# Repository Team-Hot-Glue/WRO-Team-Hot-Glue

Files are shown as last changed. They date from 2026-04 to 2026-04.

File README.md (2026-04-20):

# WRO-KU-STEAM-Hot-Glue

Hello and welcome to our repository :D

Here you will find all the code and CAD files for our robot, as well as the engineering journal that dives into how we made it.

**Assembly instructions**

**1)** In **CAD files -> Current_build** there is a .step file of the full robot assembly. It contains all the custom-made parts of the chassis. You can import it into CAD software of your choice and view how the robot's fully assembled chassis must look like. We recommend using it as a reference during assembly.  

**2)** 3D Print the provided .stl files using PLA or PETG. *Note*: we also used a metal Makeblock mBot2 chassis. This chasis part can be bought on online retailers like AliExpress or just salvaged from a broken mBot2 (that's what we did). You could also 3D print the chassis and modify it as we did (written bellow). You can buy the 3D file here (just keep in mind that the plastic version is likelly going to perform worse then the metal):  https://sketchfab.com/3d-models/mbot2-chassis-36600557720d4e2c9568bb747af69cdd
* DISCLAIMER - We are not the authors of this file and are not associated with the seller of the 3D file. We just provide an option to 3D print the chassis.
  
**3)** Chassis modification. We cut off the part of the chassis..... (Coming soon)    We spray painted it with some generic white car primer, that was found in a local hardware store for cheap (painting is completely optional, we did it just for looks).
  
**4)** Order the necessary electronic components from your local electronics components shop or an online retailer. The full list and rellevant links can be found **IN THE ENGINEERING JOURNAL**

**5)** Screw in the 3D printed parts to the chassis. Most of the screws used are M4 size (later the exact sizes and amounts of each size screws will be confirmed)

**6)** Mount the electronic components to the chassis. TOF sensors will need to be screwed in, motor board doesnt need screws, it is beeing held in place by tpu stoppers (you have to 3D print them, the file is provided). Raspberry pi is beeing held to the chassis by velcro tape (similar to this, but different manufacturer: https://www.amazon.com/Adhesion-Adhesive-Interlocking-Mounting-Reclosable/dp/B0F8QH6T7F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)

**7)** Connect all the cables according to the wiring diagram: **Wiring.pdf**

**8)** Cable manage everything. We used zipties and hotglue for that, to stop the header connectors and jumpers from disconecting CA glue was used.

**9)** Enjoy your new robot, make it pretty by adding cat stickers to it (optional, but highly recommended) 

wro cat

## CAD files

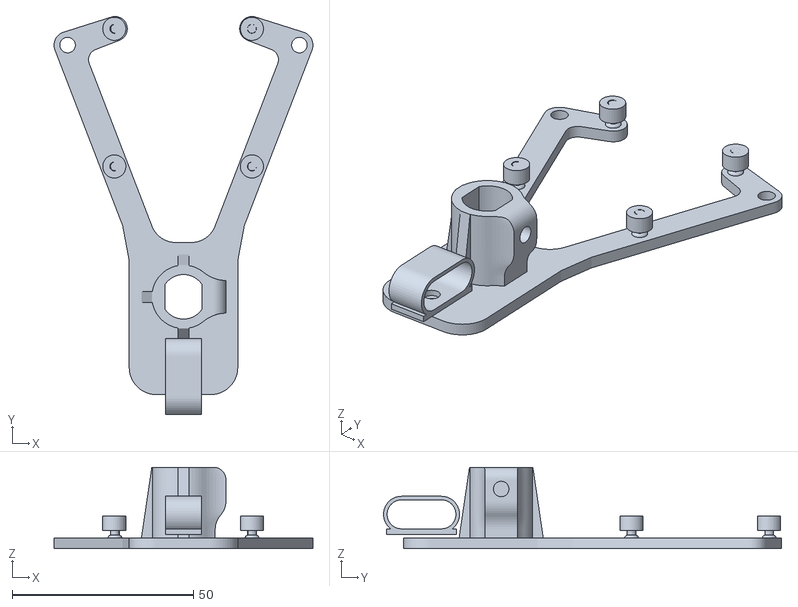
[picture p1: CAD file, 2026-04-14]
CAD files/Current_version/Files_for_printing/motor_housing_asmbl.stl
71.5 x 109.9 x 22.5

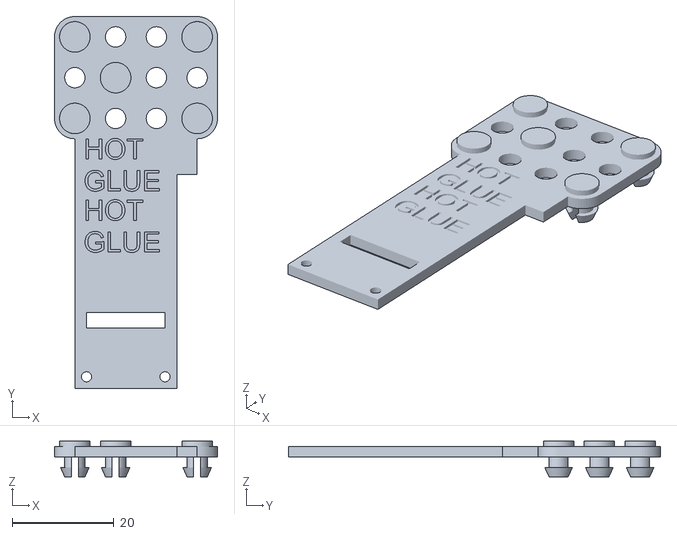
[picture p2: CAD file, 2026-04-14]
CAD files/Current_version/Files_for_printing/TOF_asmbl_right.stl
32.0 x 73.0 x 7.00

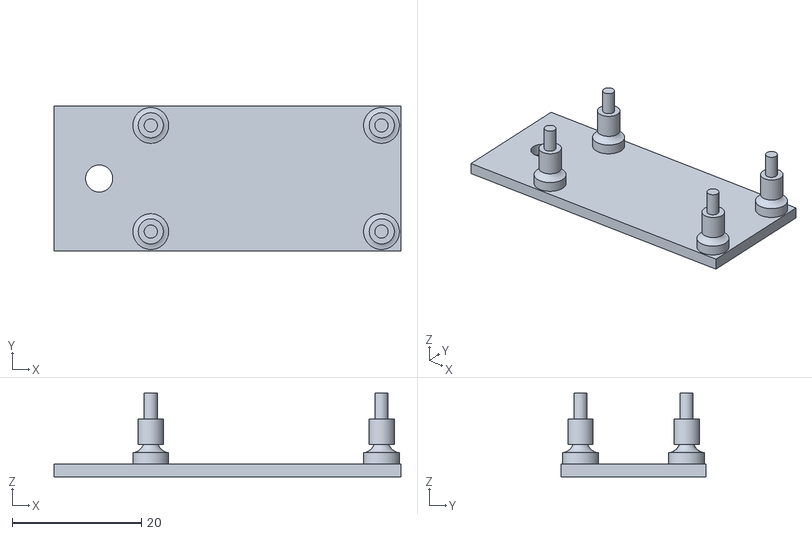
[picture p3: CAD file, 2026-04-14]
CAD files/Current_version/Files_for_printing/5v_conv_mount_asmbl.stl
53.8 x 22.5 x 13.0

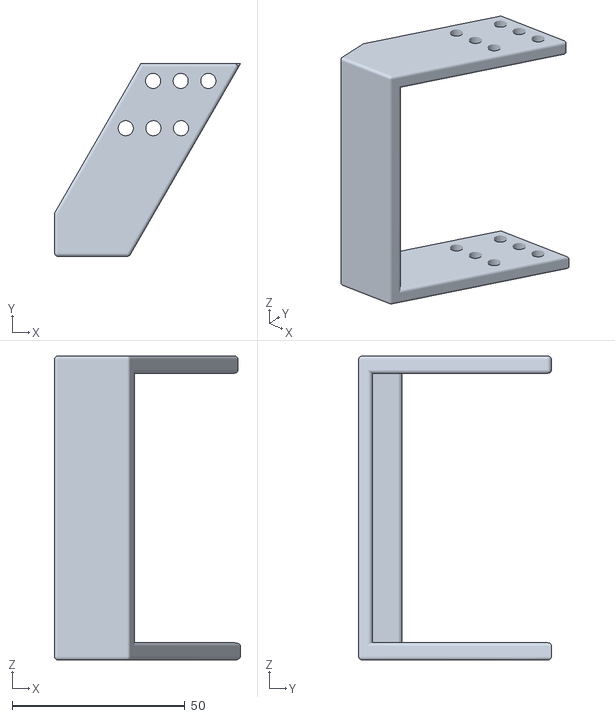
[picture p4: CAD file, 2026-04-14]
CAD files/Current_version/Files_for_printing/Battery_mount-003.stl
53.9 x 55.8 x 88.0

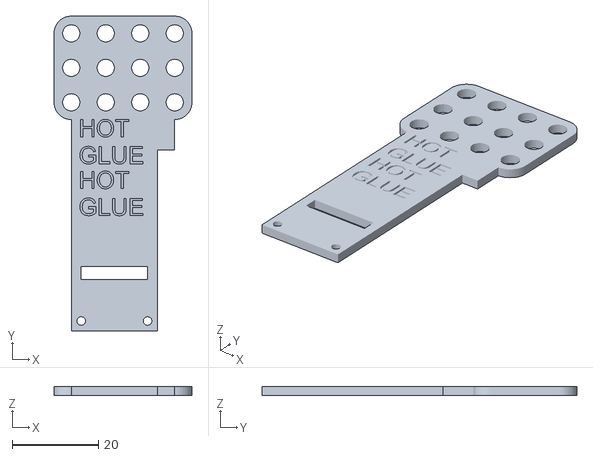
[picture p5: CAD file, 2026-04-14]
CAD files/Current_version/Files_for_printing/TOF_side.stl
32.0 x 73.0 x 2.00

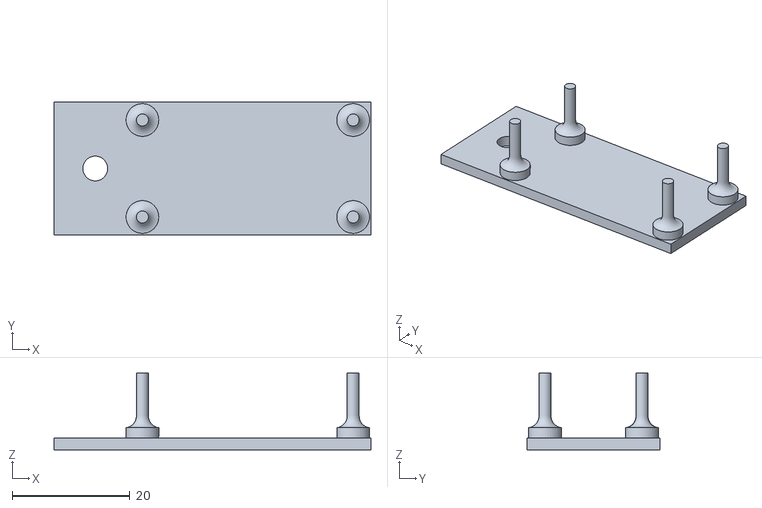
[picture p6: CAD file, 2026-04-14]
CAD files/Current_version/Files_for_printing/5v_converter_mount.stl
53.8 x 22.5 x 13.0

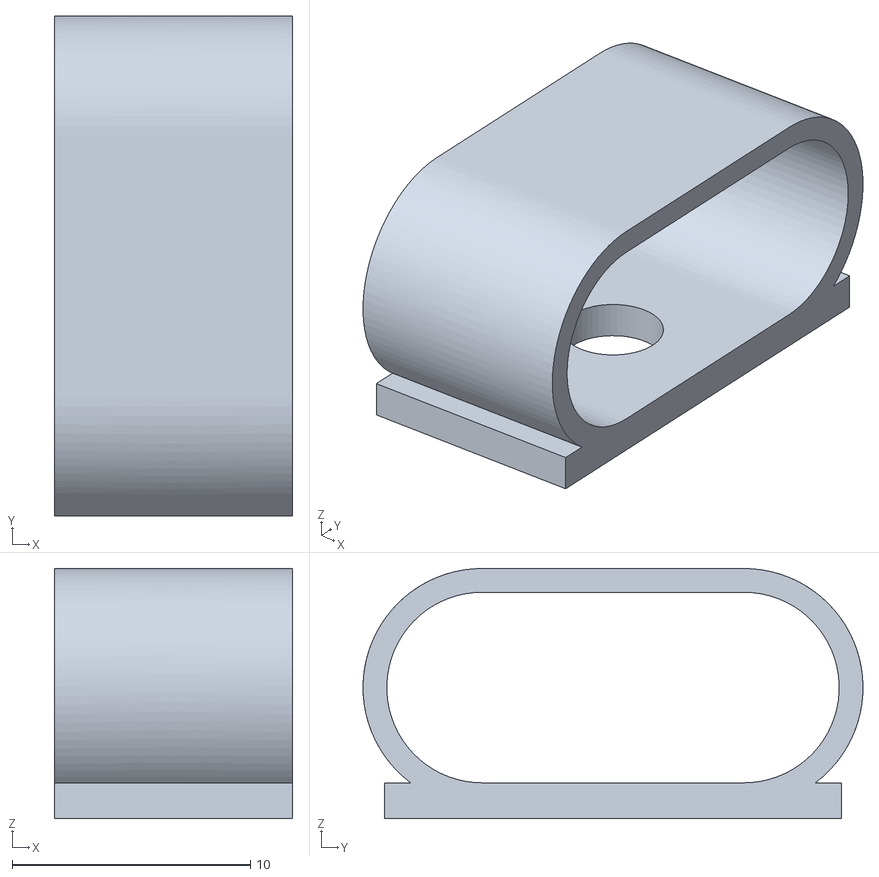
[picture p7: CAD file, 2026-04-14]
CAD files/Current_version/Files_for_printing/cable_pin_1.stl
10.0 x 21.0 x 10.5

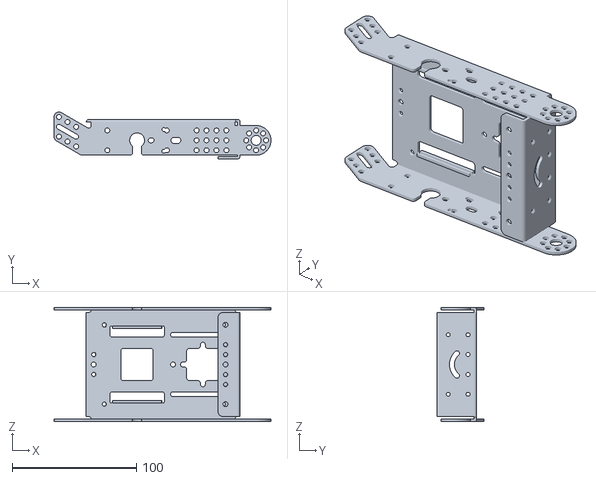
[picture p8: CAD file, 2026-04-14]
CAD files/Current_version/Files_for_printing/Chassis.stl
175.0 x 37.8 x 92.0

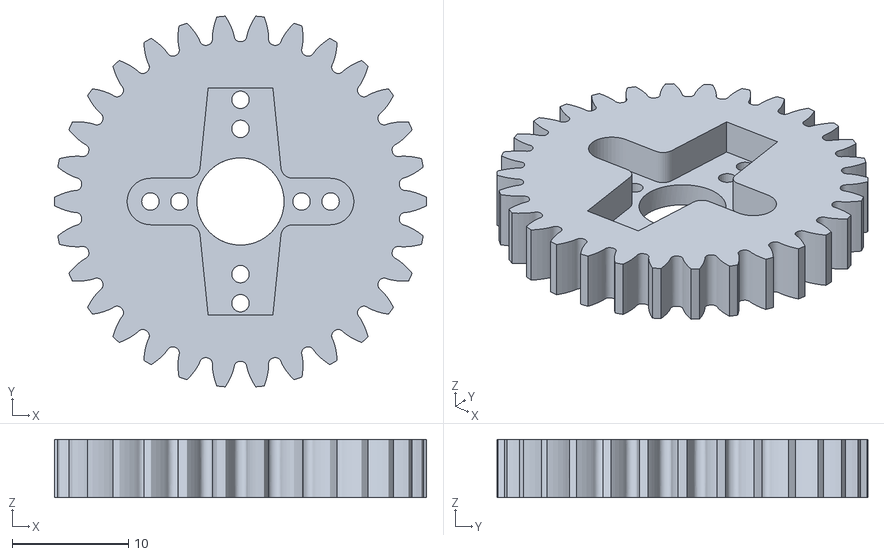
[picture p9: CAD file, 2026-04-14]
CAD files/Current_version/Files_for_printing/servo_gear-002.stl
32.0 x 31.9 x 5.00

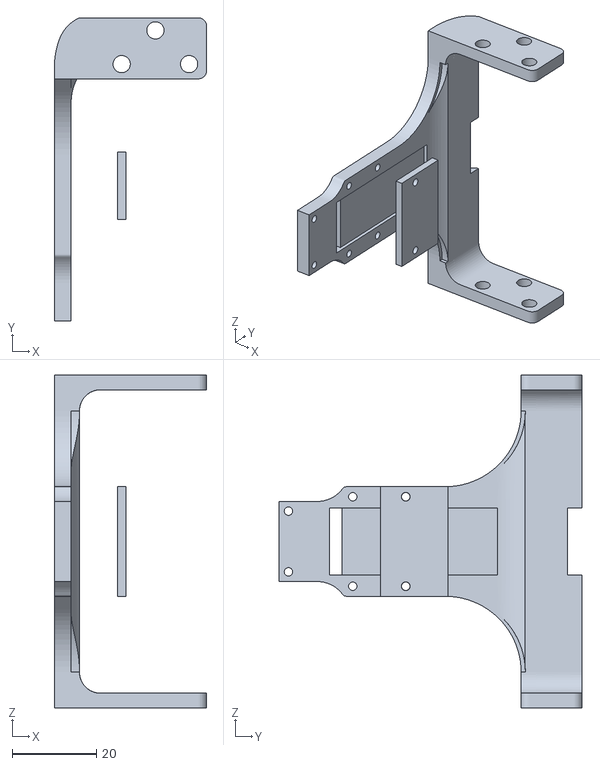
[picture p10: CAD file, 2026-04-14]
CAD files/Current_version/Files_for_printing/Camera_mount.stl
36.2 x 72.0 x 79.0

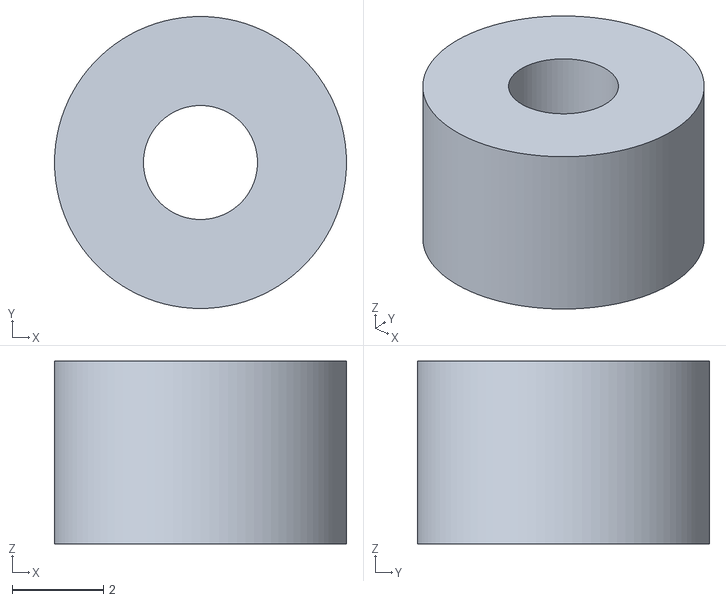
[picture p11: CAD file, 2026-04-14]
CAD files/Current_version/Files_for_printing/tpu_stopper.stl
6.40 x 6.40 x 4.00

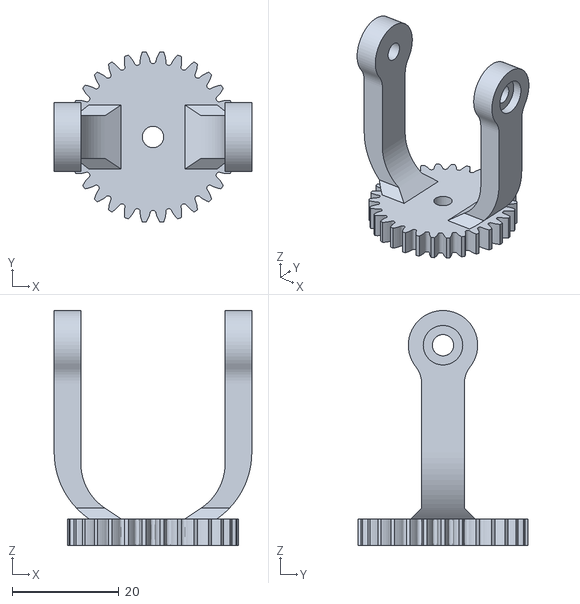
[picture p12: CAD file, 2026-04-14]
CAD files/Current_version/Files_for_printing/Spur Gear (30 teeth).stl
37.0 x 31.9 x 44.0

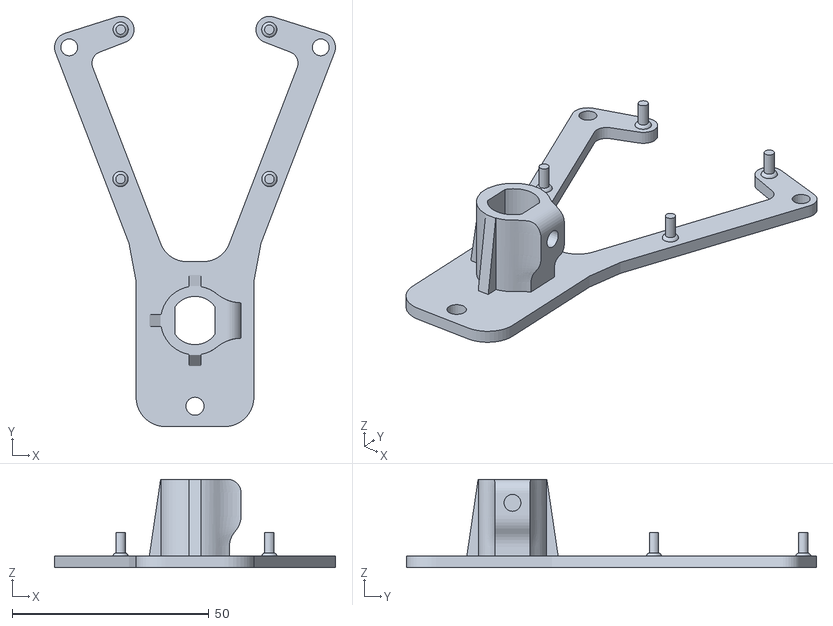
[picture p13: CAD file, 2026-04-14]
CAD files/Current_version/Files_for_printing/motor_housing_NEW.stl
71.5 x 104.4 x 22.5

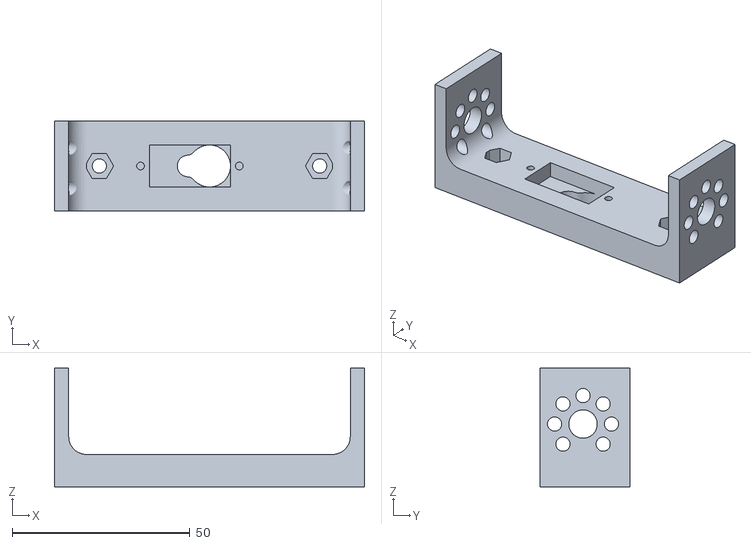
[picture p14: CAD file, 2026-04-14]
CAD files/Current_version/Files_for_printing/servo_mount_-002.stl
87.2 x 25.3 x 33.4

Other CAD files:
CAD files/Current_version/Files_for_printing/TOF_asmbl_left.stl
CAD files/Current_version/Files_for_printing/wheel_rim-002.stl
CAD files/Current_version/Files_for_printing/TOF_side_pin.stl
CAD files/Current_version/Files_for_printing/Motor_wheel_rim.stl
CAD files/Current_version/Files_for_printing/5v_converter_stopper.stl
CAD files/Current_version/Files_for_printing/Steering_V7.stl
CAD files/Current_version/Files_for_printing/wheel_gear-002.stl
CAD files/Previous_iterations/Battery_mount/Battery_mount-001.step
CAD files/Previous_iterations/Battery_mount/Battery_mount-002.step
CAD files/Previous_iterations/Battery_mount/Battery_mount-003.step
CAD files/Previous_iterations/Steering/Steering_V1.stp
CAD files/Previous_iterations/Steering/Steering_V2.stp
CAD files/Previous_iterations/Steering/Steering_V3.stp
CAD files/Previous_iterations/Steering/Steering_V4.stp
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

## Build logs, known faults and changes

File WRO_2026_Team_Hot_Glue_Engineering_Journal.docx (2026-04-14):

Team Hot Glue

Engineering Journal

WRO 2026

Lukas Mažrimas, Jokūbas Buta, Jokūbas Dargevičius

# Preface

This document is designed to explain some key aspects of the design of our team’s robot. The journal has a couple of distinct chapters, each explaining a different area of the robot’s development. Moreover, the chapters showcase the chronological order of the development, meaning that, for example, the mechanical platform was first created and then all the sensors and circuits were tailored to the existing platform. The reasoning behind this will be explained in chapter 1.

# 1. Structuring, workflow, concept

## 1.1. Team structure and workflow

Before starting any meaningful work, we took some time to map out the general ideas and assign each of us a part of the design process. Lukas was responsible for the mechanical platform, Jokūbas Buta for the general movement programming and integration, and Jokūbas Dargevičius for circuits and sensors as well as their programming.

There was, of course, a great deal of team effort and solving problems together, but giving primarily one type of work to each team member was beneficial and efficient for a multitude of reasons. Firstly, we all come from different backgrounds and have different types of experience and skillsets. Therefore, it makes sense to have the person, who is best at coding, design most of the software. It also makes sense having all the soldering done by the person who has the most experience with soldering. Moreover, a mechanical platform will be better if made by one most proficient in physics. Secondly, creating a robot is no simple feat and each of us learned a lot of new things in the process. We found it much easier for us to each concentrate on one field and do lots of in-depth research in that particular field, rather than us all trying to juggle everything at once.

## 1.2. Design process

Another thing we did in the beginning was decide on the specific electrical components and sensors to use and buy them. More about the exact choices will be explained in chapter 3, but knowing all the components in advance allowed for a better overall design and gave us time to prepare and find good hardware and software solutions for the particular “stock” components.

We chose to follow a simple and linear development path: choose and buy the sensors and other “stock” parts, make a mechanical platform, then make all the circuits and mount them and the sensors on the chassis, and, finally, program everything. This path was easy to structure and follow. However, it also created a double challenge: lots of foresight must be put into the design in the beginning, and later design elements must be flexible enough to work around existing limitations. We tried as best we can to mitigate these issues by brainstorming and agreeing on the general concept and design decisions in advance. Of course, there was still a lot of testing done during every stage of development, and many hotfixes to previous designs were made. The general concepts, however, remained unchanged.

## 1.3. Physical assembly

Designing a robot is only half of the equation – it must also be built and tested in the real world. This was made possible “Klaipėdos universiteto metodinis STEAM atviros prieigos centras (https://steam.ku.lt/lt/apie-steam-centra)”. They provided us with the ability to meet in one place and also lent us some of tools, necessary for the robot assembly (screwdrivers, screws, glue and other). Most of CAD designing and 3D printing was done at home, while all of the assembly, testing and design discussions were done during team meetings in the STEAM center.

## 1.4. Design software

In this paragraph we list all the software that we used to facilitate our workflow:

CAD design: Autodesk Fusion (https://www.autodesk.com/products/fusion-360/overview)(education license) – free for students (our team), powerful, feature rich, easy to use and customize. It also has a cloud synchronization system, that helped us effortlessly share files and make on-the-go adjustments anywhere with internet access, including the STEAM center of KU, where we would meet to work on the robot together.

Programming:

3D printer slicing: Ultimaker Cura (https://ultimaker.com/software/ultimaker-cura/) – free and open-source software, customizable and works with any FDM 3D printer.

## 1.5. Design philosophy

One of the main driving principles behind most of the design decision-making was that of the F1 design legend Collin Chapman: “Simplify, then add lightness”. We wanted to have as little moving parts, as possible, because moving parts wear and can ultimately break. We also followed another principle of his: “Rules are for the obedience of fools and interpretations of smart men.” This is to say, we were on the outlook for areas of excessive design freedom.

# 2. List of stock components used

Part | Visuals | Part code

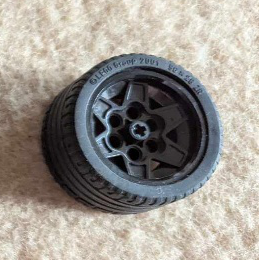
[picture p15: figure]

Front wheel tire | | Tire 43.2 x 22 ZR (44309 (https://www.bricklink.com/v2/catalog/catalogitem.page?P=44309))

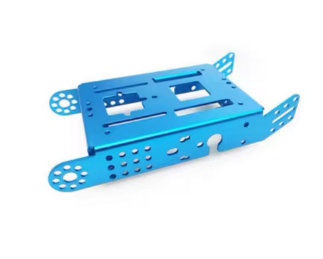
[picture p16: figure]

Chassis | | Metal chassis for Makeblock mBot2 (https://www.aliexpress.com/item/1005008112495776.html)

The reasoning behind each choice will be explained later on.

# 3. Mechanical platform

## 3.1. Overview

The mechanical platform consists of three main areas: steering system, driving axle and the chassis that connects them. We agreed to make a conventional rear-wheel-drive system: front wheels are designated to steering, and rear wheels are driven. This type of package is simple and effective.

## 3.2. Steering

The principal requirements that we had for our steering were compactness and high steering angles. High steering angles allow for smaller turning radius, which is of utmost importance in the challenge for optimal navigation around circuit and good parking performance. Compactness allows for a smaller overall footprint of the robot and also leaves space for future drivetrain, sensor and electronics placement.

Below are the design iterations of the steering system and their descriptions:

Iteration | Visuals | Description

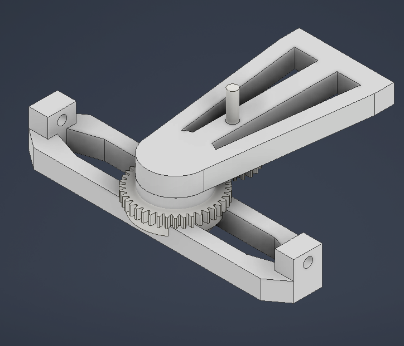
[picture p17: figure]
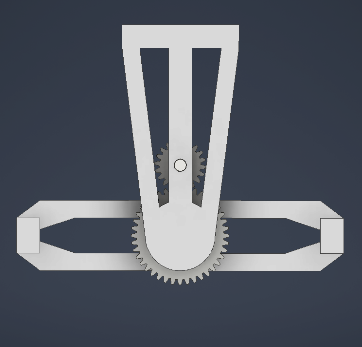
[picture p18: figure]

V1 | | The very first design. A very simple concept, in which the entire front axle is being turned around a pivot. Scrapped due to excessive space needed and instability of the platform when the entire front axle is at an angle with the rest of the body.

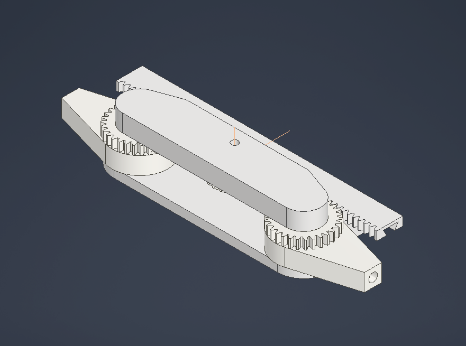
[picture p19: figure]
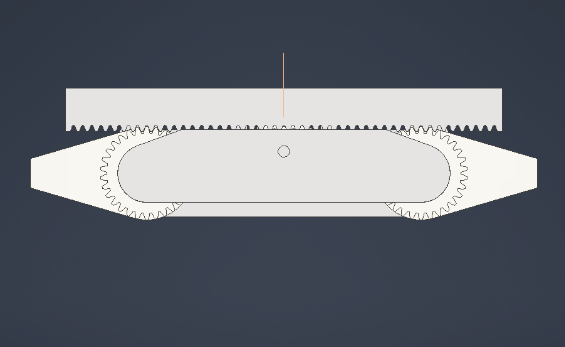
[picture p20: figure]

V2 | | The concept of this version was to pivot the wheel hubs around their respective axis, and rotate them simultaneously with a shared rack. Scrapped due to high friction and general bulkiness of the design.

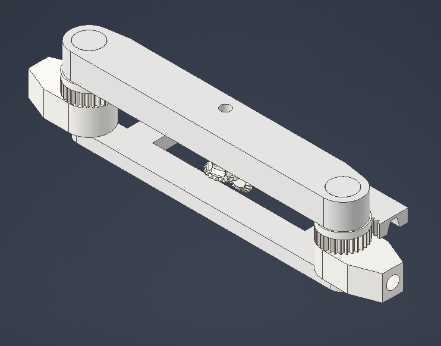
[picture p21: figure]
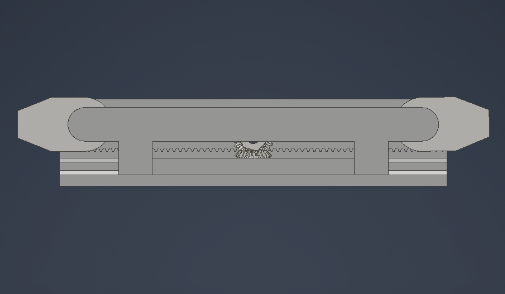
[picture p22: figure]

V3 | | An evolution of the V2 design. Bevel gears were added to have a possibility of connecting a servo motor. Scrapped due to the complications of integrating a servo motor well, as well as the steering angle not being sufficient.

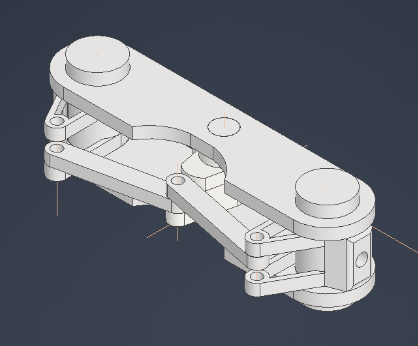
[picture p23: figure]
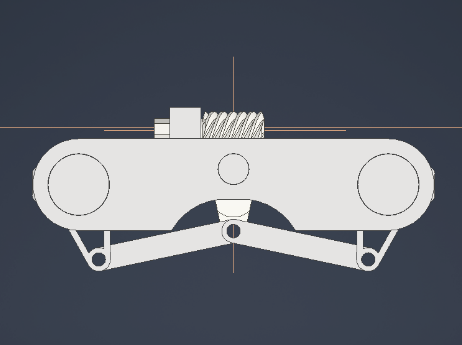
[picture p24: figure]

V4 | | Brand new concept: have a worm gear connect to a lever arm, that would in turn move control arms that connect to wheel hubs. This design allowed sufficient space for the servo motor. Scrapped due to poor steering angle and the design being too many moving parts taking up too much space.

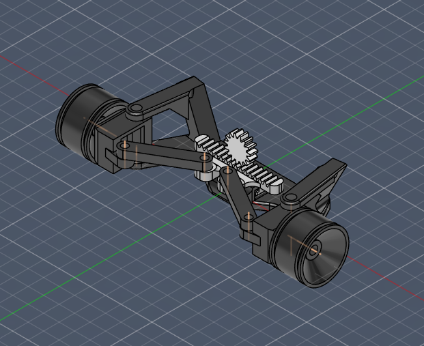
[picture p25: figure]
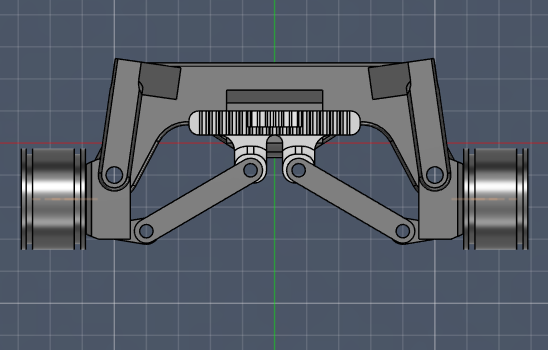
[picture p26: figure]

V5 | | An attempt at a rack and pinion design concept. Now the steering system was more compact and had less general friction. Through extreme control arm attachment points high steering angles were achieved. Scrapped due to non-existent stability when steering (a direct consequence of control arm attachment), and poor robustness of the system (control arm attachment “ears” would break off). Custom wheel rims for the tires in use were created (this part would be used in later designs as well)

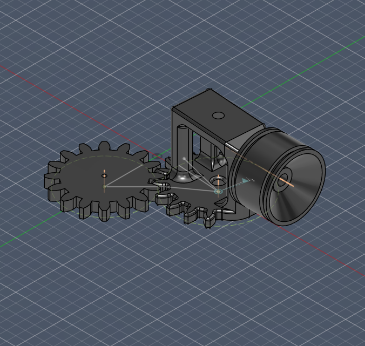
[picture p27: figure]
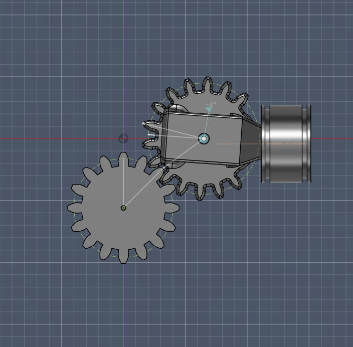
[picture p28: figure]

V6 | | A test of a (yet another) new concept. The concept is as follows: have 3 spur gears connected together. The middle one attached to the servo and being driven. The gears on the side have wheel hubs on them and attach to the wheels. All three gears move in sync. This concept was evolved further into the V7 variant.

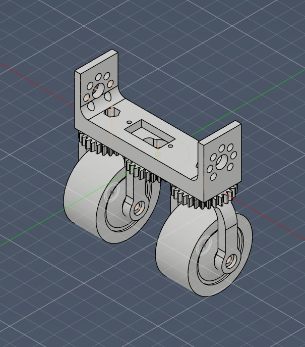
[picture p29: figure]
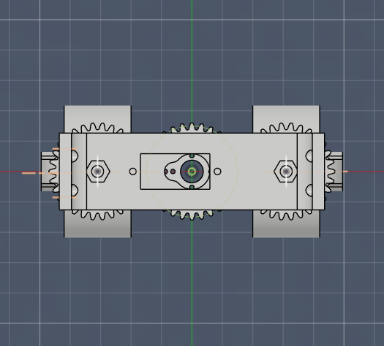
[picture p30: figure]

V7 | | A full, working adaptation of V6 concept. Features a mounting point for the servo motor. Wheel hubs designed for minimum footprint and optimal leverages. The exact dimensions and mounting hole were tailored to the chassis that we decided to use. Custom wheel rims adjusted to fit wheel hubs.

During the design process of the steering system, at iteration V5, the tire specification to be used was decided. We wanted simple tires, that are abundant on the market. For steering, wide tires were required, as there had to be sufficient grip for sharp turning maneuvers. Also, the tires had to have a small vertical footprint. That is because the front wheels weren’t going to be driven, so the wheel size was inconsequential in this regard, but smaller wheels allowed for a more compact design, which is one of the principal requirements of our steering system.

We considered various LEGO® tires, as all of us had plenty of them at home (so, the effective cost of using one would be 0), and they were made out of a sufficiently grippy material for our purposes.

After trying out multiple variants, we found that, out of the models that we had, tire 43.2 x 22 ZR fit our needs best.

It became clear immediately, that the stock wheel rims wouldn’t work for us, as we needed round holes, whereas the LEGO® rims all have cross shaped holes. Because of that, we designed our own hubs.

The custom wheel hubs also underwent significant evolution, that we showcase here:

Designed for steering version | Visuals | Constraining features

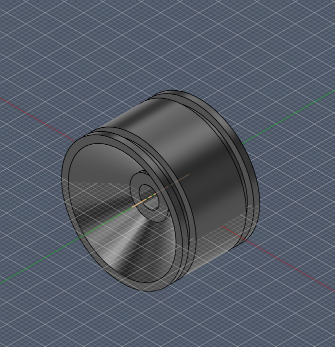
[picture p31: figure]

V5 | | Mount on the side, of the rotating assembly, have minimum weight.

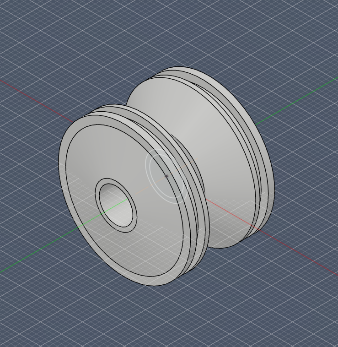
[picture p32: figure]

V7 | | Mount in the middle of the rotating fork, center the wheel, and have minimum weight

## 3.3. Chassis

The choice of a chassis was affected not only by engineering needs, but also other surrounding factors at the time. Our school has a big fleet of Makeblock mBot2® robots. During the time of construction of our robot, one of them broke down completely. After an inspection, the school wrote it off as unusable. Thus, we got an opportunity to make use of its part if we wanted to. Indeed, the mBot2® was of use to us. Firstly, it is made of metal, so it will not break during any use case. Secondly, it has, many perforations for mounting various sensors and attachments, so it allows for good design flexibility. Also, there is an economical and environmental benefit as well, because using this chassis didn’t cost us any money, and didn’t allow a perfectly usable metal component be put to waste. That is how we chose our main chassis.

## 3.4. Driven axle

The biggest possible problem for the rear axle is the fact, as per the rules, that both rear wheels have to be connected to the same driving motor. This means that both wheels will always have the same angular velocity of rotation. That is bad for stable cornering, as from simple geometry, the rotational speeds of rear wheels must differ if the wheels are to not slip, because the outer wheel has to cover a greater distance in the same amount of time. Therefore, due to the formulation of the rules, any compliant rear axle by design will have some wheel slip during cornering.

Again, from simple geometry, the wider the rear axle, the bigger rotation speed difference is needed for the wheels not to slip. Therefore, in our situation, having as narrow rear axle as possible is beneficial, due to the fact, that there will be less of a speed difference between the rear wheels, so less slip, so the axle will be more predictable and under control. The downside of such a configuration is that the platform will be vulnerable to falling on its side if the turn is too sharp. That can be mitigated by having a lower center of gravity and a wide, stable front axle.

While searching for a suitable motor, we stumbled upon a curious offering on Aliexpress – an N30 dual shaft motor (https://www.aliexpress.com/item/1005009087328271.html?curPageLogUid=cAlrlbEzFobY). It already had a built-in gearbox and two shafts for mounting the wheels. Besides, the whole assembly was pretty narrow – only 10 mm. This was a perfect option for us, so we decided to use it as a rear axle.

For the wheels, we again chose to go for LEGO® tires, as they we have plenty different options at home and these tires are made of durable material with good traction. As for the specific tire, we went for Tire Technic Wedge Belt Wheel (https://www.bricklink.com/v2/catalog/catalogitem.page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,%20Tire%20&%20Tread%5D), because they were extremely narrow, and this would further minimize tire slip when cornering. Again, like with the front wheels, we needed to design our own wheel rims, that fit the motor gearbox shafts.

In order to improve packaging, we decided to use the motor as a stressed member of the chassis. A simple attachment that mimicked the shape of the motor’s outer shell was made to connect the metal frame with the motor. Due to the dimensions of the steering system, the motor had to be placed in a vertical orientation in order for the chassis to be level with the ground. The attachment also features a screw driven clamp for securing the motor in place. It must be said, that although simple and effective, the attachment has a minor flaw – tightening the clamp screw too tight will permanently damage the motor. This, thankfully can be easily avoided and the clamp still holds the motor in place securely.

## 3.5. Design summary, tradeoffs

Finally, we want to take one last look at overall design of the mechanical platform that we made and its main features as well as tradeoffs.

The goal of having extremely high steering angles was achieved. Both the design of the front and rear axles enhances this feature, as the rear axle is so narrow and its wheels so slim that it effectively works like one center-mounted rear wheel.

This agility, though, comes at a cost. The inherent stability of the robot isn’t great, and it may be prone to falling over in sharp turns if the center of mass is put too high up. Therefore, an additional challenge of designing electrical circuits is lowering all the heavy components as low as possible.

# 4. Circuit design and sensors

## 4.1. Overview

## 4.2. Processing units

## 4.3. Sensors and their placement

## 4.4. Battery and power budget

## 4.5. Circuits and packaging

## 4.6. Design summary, tradeoffs

# 5. Software

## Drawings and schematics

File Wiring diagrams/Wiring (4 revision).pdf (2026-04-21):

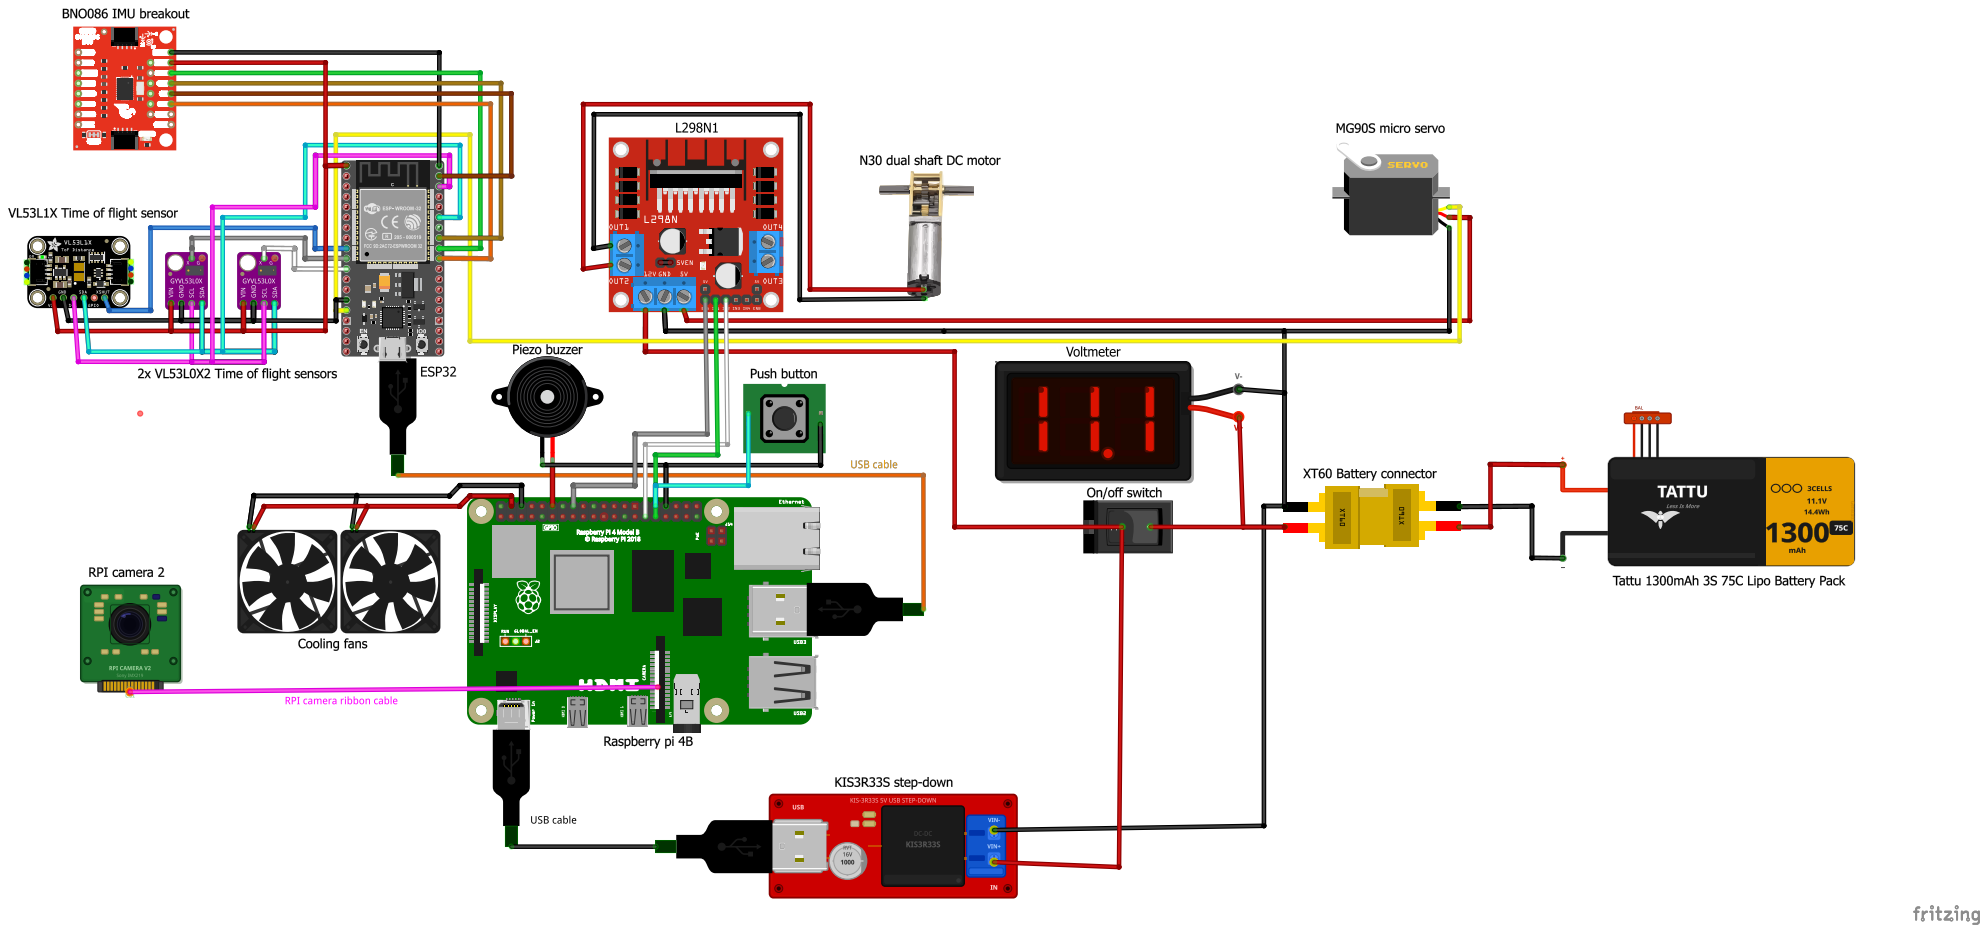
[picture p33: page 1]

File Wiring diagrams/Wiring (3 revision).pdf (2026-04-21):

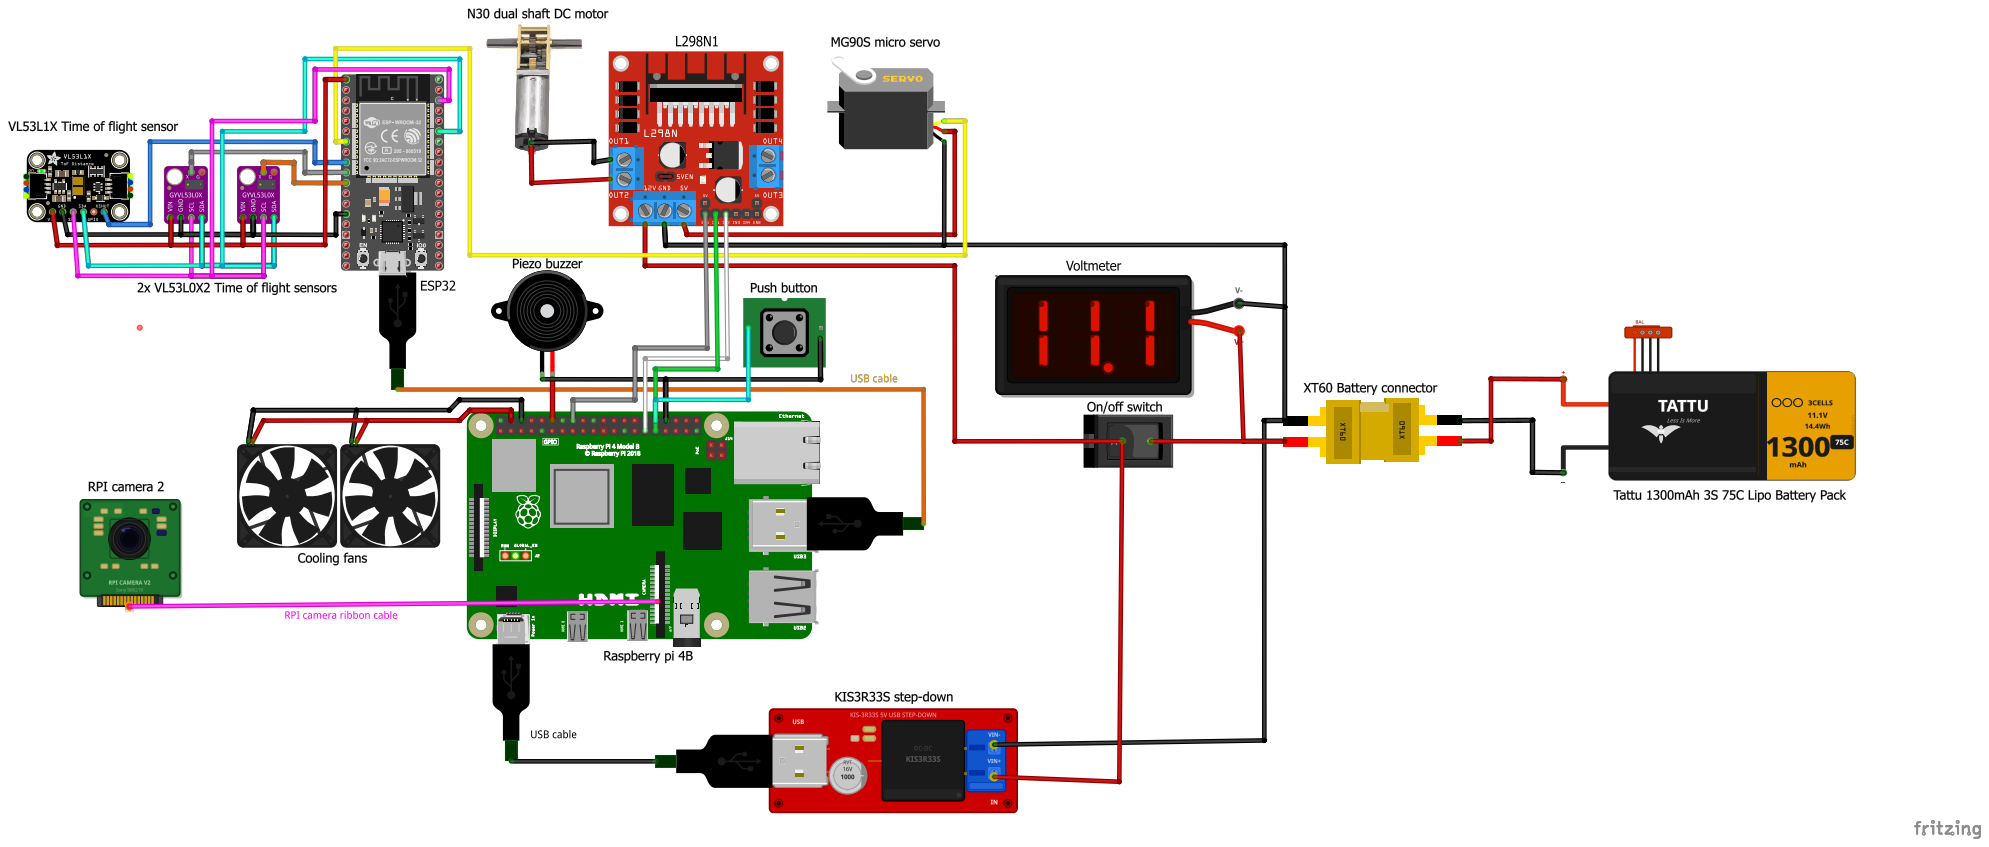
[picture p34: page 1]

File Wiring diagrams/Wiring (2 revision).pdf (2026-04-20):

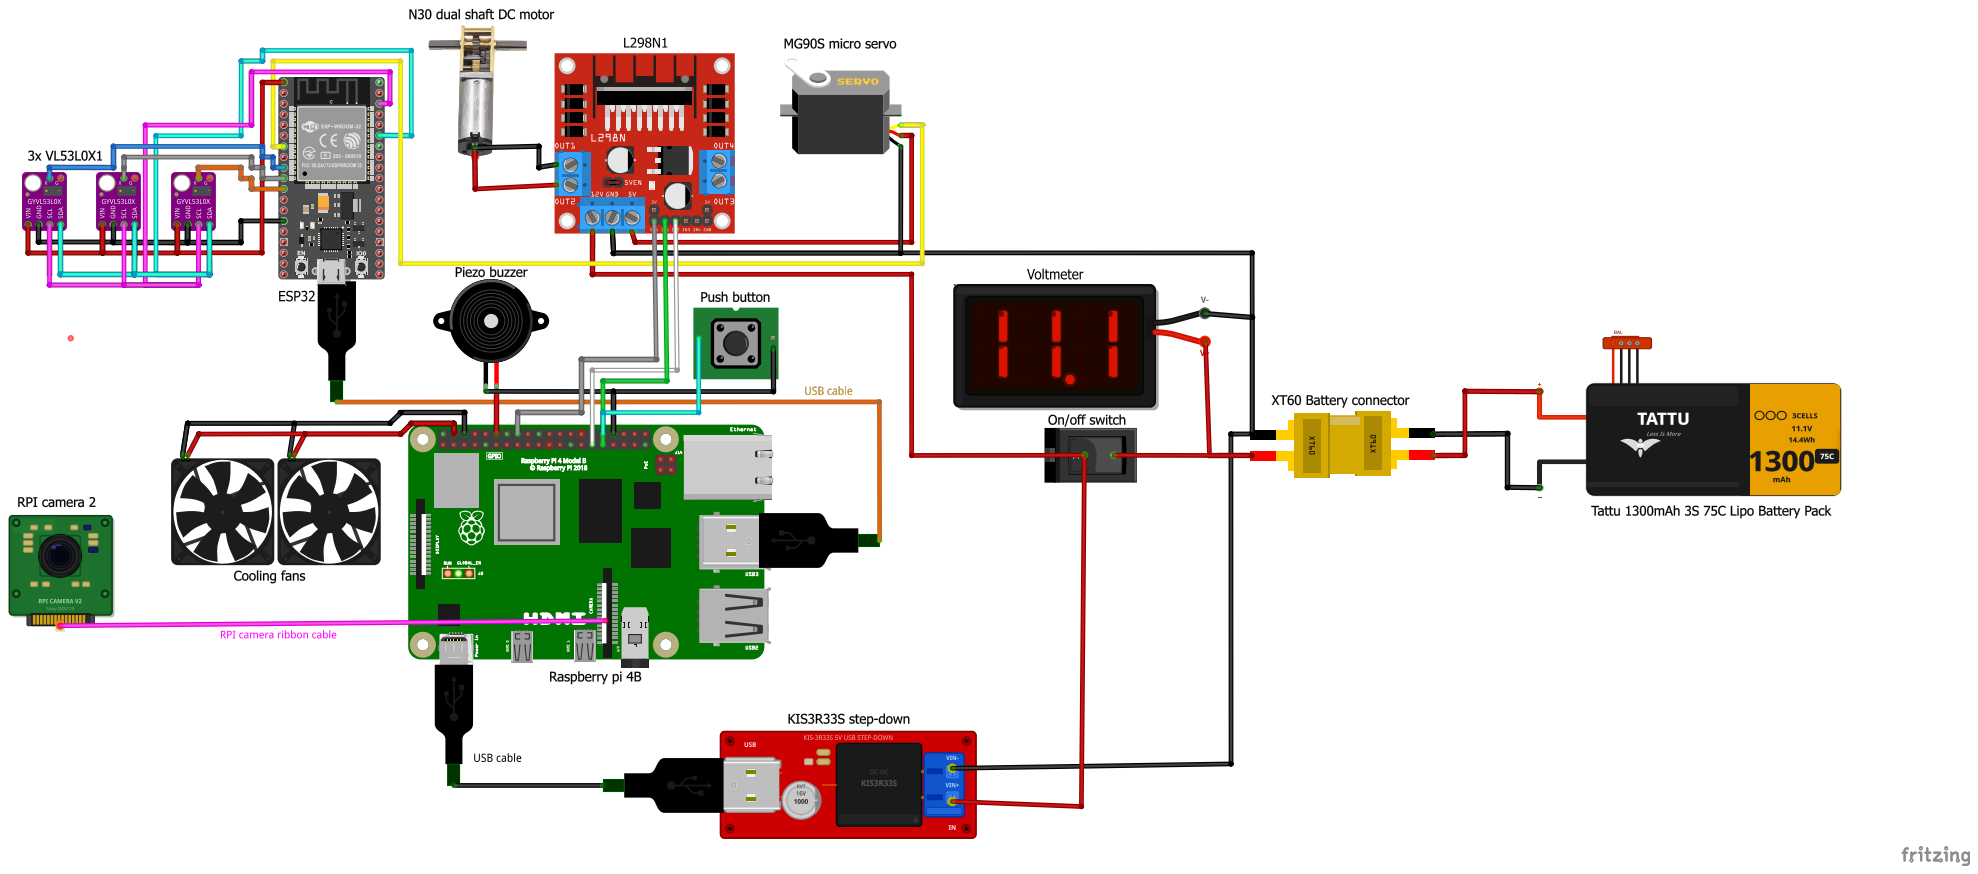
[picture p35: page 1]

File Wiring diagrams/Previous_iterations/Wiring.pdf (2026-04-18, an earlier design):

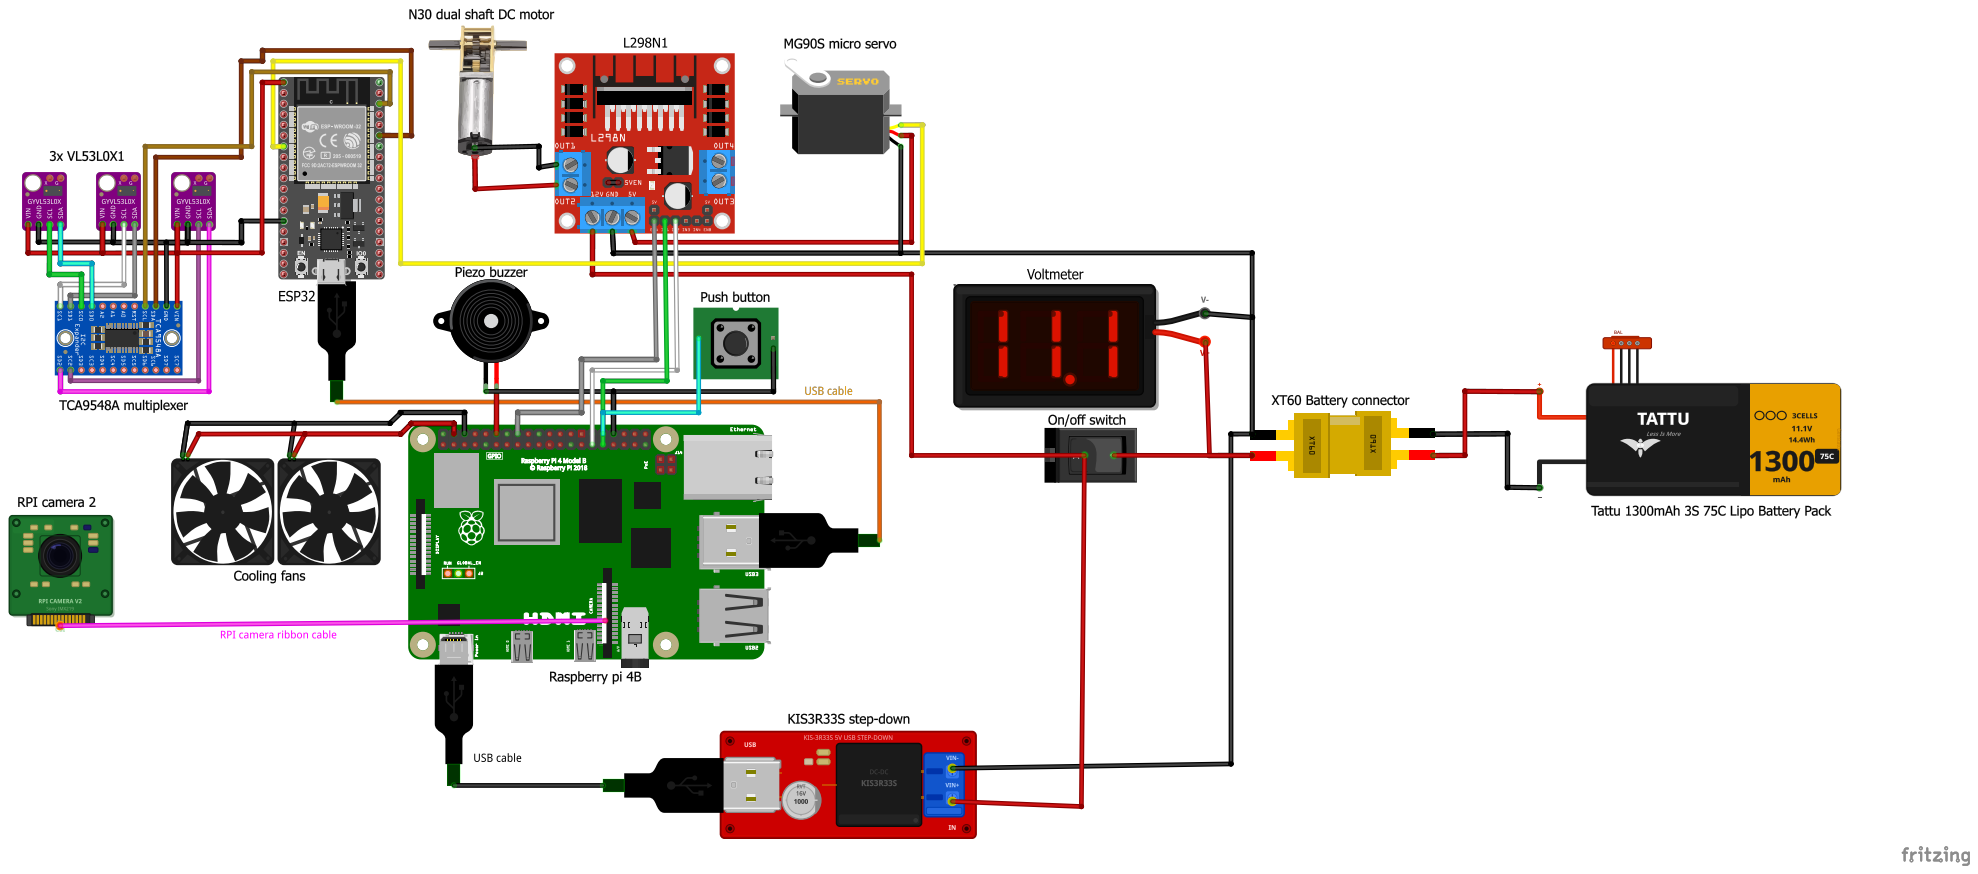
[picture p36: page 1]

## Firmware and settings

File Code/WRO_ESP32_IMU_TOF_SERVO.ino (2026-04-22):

/*─────────────────────────────────────────────────────────────────────────────
  TOF, Servo and BNO086 IMU

  Serial output (115200 baud) – one CSV line per tick at PRINT_HZ:

  d0,d1,d2,ax,ay,az,gx,gy,gz,roll,pitch,yaw

  d0/d1/d2 : ToF distances in mm
  ax/ay/az : linear acceleration  in m/s²  
  gx/gy/gz : gyroscope (rad/s) 
  roll, pitch, yaw : Euler's angles.          

  Commands received from RPi over USB Serial:
  a<angle>   – move servo to angle 0-180
  start      – trigger servo sequence
 ─────────────────────────────────────────────────────────────────────────────*/

#include <Wire.h>
#include <Adafruit_VL53L0X.h>
#include <Adafruit_VL53L1X.h>

#include <ESP32Servo.h>

#include <SparkFun_BNO08x_Arduino_Library.h>

#define SERVO_PIN    13
#define XSHUT_L0X_0  25   // sensor[0] VL53L0X
#define XSHUT_L1X    26   // sensor[1] VL53L1X
#define XSHUT_L0X_2  27   // sensor[2] VL53L0X

#define BNO086_ADDR  0x4A

#define ADDR_L0X_0   0x30
#define ADDR_L1X     0x29
#define ADDR_L0X_2   0x32

#define FILTER_WINDOW   5      // ToF moving-average window
#define PRINT_HZ        50     // Serial output rate (Hz)

// IMU report interval in microseconds – 10 000 µs = 100 Hz
#define IMU_REPORT_INTERVAL_US  10000

// BNO086
BNO08x imu;
bool imuOK = false;

float imu_ax = 0, imu_ay = 0, imu_az = 0;   // linear acceleration
float imu_gx = 0, imu_gy = 0, imu_gz = 0;   // gyroscope
float imu_roll = 0, imu_pitch = 0, imu_yaw = 0; //Euler's angles

void imu_setup() {
  if (!imu.begin(BNO086_ADDR, Wire, -1, -1)) {
    Serial.println("[ERROR] BNO086 not found – check wiring and I2C address");
    imuOK = false;
    return;
  }

  imu.enableLinearAccelerometer(IMU_REPORT_INTERVAL_US);

  imu.enableGyro(IMU_REPORT_INTERVAL_US);

  imu.enableRotationVector(IMU_REPORT_INTERVAL_US);

  imuOK = true;
  Serial.printf("[OK]    BNO086 @ 0x%02X  (accel + gyro + rot @ %u µs)\n",
                BNO086_ADDR, IMU_REPORT_INTERVAL_US);
}

void imu_read() {
  if (!imuOK) return;
  while (imu.getSensorEvent()) {
    if(imu.getSensorEventID() == SENSOR_REPORTID_LINEAR_ACCELERATION) {
      imu_ax = imu.getLinAccelX();
      imu_ay = imu.getLinAccelY();
      imu_az = imu.getLinAccelZ();
    }

    if(imu.getSensorEventID() == SENSOR_REPORTID_GYROSCOPE_CALIBRATED){
      imu_gx = imu.getGyroX();
      imu_gy = imu.getGyroY();
      imu_gz = imu.getGyroZ();
    }

    if (imu.getSensorEventID() == SENSOR_REPORTID_ROTATION_VECTOR){
      imu_roll = (imu.getRoll()) * 180.0 / PI;
      imu_pitch = (imu.getPitch()) * 180.0 / PI;
      imu_yaw = (imu.getYaw()) * 180.0 / PI;
    }
  }
}

Adafruit_VL53L0X l0x_0;
Adafruit_VL53L1X l1x = Adafruit_VL53L1X(XSHUT_L1X);
Adafruit_VL53L0X l0x_2;

bool sensorOK[3] = {false, false, false};
uint16_t distances[3] = {INVALID_MM, INVALID_MM, INVALID_MM};

uint16_t filterBuf[3][FILTER_WINDOW] = {};
uint8_t  filterIdx[3]  = {0, 0, 0};
uint8_t  filterFill[3] = {0, 0, 0};

uint16_t movingAverage(uint8_t s, uint16_t val) {
  filterBuf[s][filterIdx[s]] = val;
  filterIdx[s] = (filterIdx[s] + 1) % FILTER_WINDOW;
  if (filterFill[s] < FILTER_WINDOW) filterFill[s]++;

  uint32_t sum = 0;
  for (uint8_t i = 0; i < filterFill[s]; i++) {
    uint8_t pos = (filterIdx[s] + FILTER_WINDOW - 1 - i) % FILTER_WINDOW;
    sum += filterBuf[s][pos];
  }
  return (uint16_t)(sum / filterFill[s]);
}

static bool reassignL1XAddress(uint8_t newAddr7bit) {
  Wire.beginTransmission(0x29);
  Wire.write((uint8_t)0x00);
  Wire.write((uint8_t)0x01);
  Wire.write((uint8_t)(newAddr7bit << 1));
  if (Wire.endTransmission() != 0) return false;
  delay(5);
  return true;
}

void tof_setup() {
  Serial.println("[BOOT] Initialising TOF sensors...");

  pinMode(XSHUT_L0X_0, OUTPUT); digitalWrite(XSHUT_L0X_0, LOW);
  pinMode(XSHUT_L1X,   OUTPUT); digitalWrite(XSHUT_L1X,   LOW);
  pinMode(XSHUT_L0X_2, OUTPUT); digitalWrite(XSHUT_L0X_2, LOW);
  delay(10);

  digitalWrite(XSHUT_L0X_0, HIGH);
  delay(15);
  if (!l0x_0.begin(0x29, false, &Wire)) {
    Serial.println("[ERROR] sensor[0] VL53L0X");
  } else {
    l0x_0.setAddress(ADDR_L0X_0);
    l0x_0.configSensor(Adafruit_VL53L0X::VL53L0X_SENSE_HIGH_SPEED);
    l0x_0.startRangeContinuous();
    sensorOK[0] = true;
    Serial.printf("[OK]    sensor[0] VL53L0X @ 0x%02X\n", ADDR_L0X_0);
  }

  digitalWrite(XSHUT_L0X_2, HIGH);
  delay(15);
  if (!l0x_2.begin(0x29, false, &Wire)) {
    Serial.println("[ERROR] sensor[2] VL53L0X");
  } else {
    l0x_2.setAddress(ADDR_L0X_2);
    l0x_2.configSensor(Adafruit_VL53L0X::VL53L0X_SENSE_HIGH_SPEED);
    l0x_2.startRangeContinuous();
    sensorOK[2] = true;
    Serial.printf("[OK]    sensor[2] VL53L0X @ 0x%02X\n", ADDR_L0X_2);
  }

  digitalWrite(XSHUT_L1X, HIGH);
  delay(150);
  if (!l1x.begin(0x29, &Wire)) {
    Serial.print("[ERROR] sensor[1] VL53L1X, status: ");
    Serial.println(l1x.vl_status);
    sensorOK[1] = false;
  } else {
    l1x.setTimingBudget(20);
    l1x.startRanging();
    sensorOK[1] = true;
    Serial.println("[OK]    sensor[1] VL53L1X @ 0x29");
  }
}

inline void readL0X(uint8_t idx, Adafruit_VL53L0X &sensor) {
  if (!sensorOK[idx] || !sensor.isRangeComplete()) return;
  uint16_t raw = sensor.readRange();
  distances[idx] = (raw == 0 || raw >= 8190) ? INVALID_MM : movingAverage(idx, raw);
}

inline void readL1X() {
  if (!sensorOK[1]) return;
  if (l1x.dataReady()) {
    int16_t raw = l1x.distance();
    l1x.clearInterrupt();
    distances[1] = (raw <= 0 || raw > 4000) ? INVALID_MM : movingAverage(1, (uint16_t)raw);
  }
}

// Servo
Servo servo;
int servoPosition = 105;
bool servoSequenceActive = false;
unsigned long servoTimer = 0;
int servoStep = 0;

void servo_setup() {
  ESP32PWM::allocateTimer(0);
  servo.setPeriodHertz(50);
  servo.attach(SERVO_PIN, 1000, 2000);
  servo.write(servoPosition);
}

void updateServoSequence() {
  if (!servoSequenceActive) return;
  unsigned long now = millis();
  switch (servoStep) {
    case 0:
      servo.write(0);
      servoTimer = now;
      servoStep  = 1;
      break;
    case 1:
      if (now - servoTimer >= 200) {
        servo.write(105);
        servoTimer = now;
        servoStep  = 2;
      }
      break;
    case 2:
      if (now - servoTimer >= 300) {
        servoSequenceActive = false;
        servoStep = 0;
        Serial.println("[SERVO] done");
      }
      break;
  }
}

// Serial command handling

String serialBuffer = "";

void processCommand(String cmd) {
  cmd.trim();
  if (cmd.startsWith("a")) {
    int angle = constrain(cmd.substring(1).toInt(), 0, 180);
    servo.write(angle);
    servoPosition = angle;
  } else if (cmd.equalsIgnoreCase("start")) {
    servoSequenceActive = true;
    servoStep = 0;
    Serial.println("[SERVO] start");
  }
}

void handleSerial() {
  while (Serial.available()) {
    char c = Serial.read();
    if (c == '\n' || c == '\r') {
      if (serialBuffer.length()) {
        processCommand(serialBuffer);
        serialBuffer = "";
      }
    } else {
      serialBuffer += c;
    }
  }
}

void setup() {
  Serial.begin(115200);

  pinMode(XSHUT_L0X_0, OUTPUT); digitalWrite(XSHUT_L0X_0, LOW);
  pinMode(XSHUT_L1X,   OUTPUT); digitalWrite(XSHUT_L1X,   LOW);
  pinMode(XSHUT_L0X_2, OUTPUT); digitalWrite(XSHUT_L0X_2, LOW);

  Wire.begin(21, 22);       // SDA=21, SCL=22
  Wire.setClock(400000);    

  tof_setup();
  imu_setup();
  servo_setup();

  Serial.println("[READY]");
}

static unsigned long lastPrint = 0;

void loop() {
  handleSerial();
  updateServoSequence();

  readL0X(0, l0x_0);
  readL1X();
  readL0X(2, l0x_2);
  imu_read();

  unsigned long now = millis();
  if (now - lastPrint >= (1000UL / PRINT_HZ)) {
    lastPrint = now;
    Serial.print(distances[0]); Serial.print(',');
    Serial.print(distances[1]); Serial.print(',');
    Serial.print(distances[2]); Serial.print(',');
    Serial.print(imu_ax, 2);    Serial.print(',');
    Serial.print(imu_ay, 2);    Serial.print(',');
    Serial.print(imu_az, 2);    Serial.print(',');
    Serial.print(imu_gx, 4);    Serial.print(',');
    Serial.print(imu_gy, 4);    Serial.print(',');
    Serial.print(imu_gz, 4);    Serial.print(',');
    Serial.print(imu_roll, 1);  Serial.print(',');
    Serial.print(imu_pitch, 1); Serial.print(',');
    Serial.println(imu_yaw, 1);   
  }
}

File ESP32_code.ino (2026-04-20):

#include <Wire.h>
#include <Adafruit_VL53L0X.h>
#include <ESP32Servo.h>

#define NUM_SENSORS 3
#define SERVO_PIN   18

#define FILTER_WINDOW 3

const uint8_t xshutPins[NUM_SENSORS] = {25, 26, 27};

const uint8_t sensorAddr[NUM_SENSORS] = {0x30, 0x31, 0x32};

Adafruit_VL53L0X sensors[NUM_SENSORS];

uint16_t distances[NUM_SENSORS] = {0};


uint16_t filterBuffer[NUM_SENSORS][FILTER_WINDOW] = {0};
uint8_t filterIndex = 0;

Servo servo;
int servoPosition = 105;

String serialBuffer = "";

bool servoSequenceActive = false;
unsigned long servoTimer = 0;
int servoStep = 0;

uint16_t movingAverage(uint8_t s, uint16_t val) {
  filterBuffer[s][filterIndex] = val;

  uint32_t sum = 0;
  for (int i = 0; i < FILTER_WINDOW; i++) {
    sum += filterBuffer[s][i];
  }
  return sum / FILTER_WINDOW;
}

void handleSerial() {
  while (Serial.available()) {
    char c = Serial.read();

    if (c == '\n' || c == '\r') {
      if (serialBuffer.length()) {
        processCommand(serialBuffer);
        serialBuffer = "";
      }
    } else {
      serialBuffer += c;
    }
  }
}

void processCommand(String cmd) {
  cmd.trim();

  if (cmd.equalsIgnoreCase("start")) {
    servoSequenceActive = true;
    servoStep = 0;
    Serial.println("[SERVO] start");
  }
  else if (cmd.startsWith("a")) {
    int angle = constrain(cmd.substring(1).toInt(), 0, 180);
    servo.write(angle);
    servoPosition = angle;
  }
}

void updateServoSequence() {
  if (!servoSequenceActive) return;

  unsigned long now = millis();

  if (servoStep == 0) {
    servo.write(0);
    servoTimer = now;
    servoStep = 1;
  }
  else if (servoStep == 1 && now - servoTimer >= 200) {
    servo.write(105);
    servoTimer = now;
    servoStep = 2;
  }
  else if (servoStep == 2 && now - servoTimer >= 300) {
    servoSequenceActive = false;
    servoStep = 0;
    Serial.println("[SERVO] done");
  }
}

void tof_setup() {
  Serial.println("[BOOT] Init VL53L0X (no mux)...");

  for (int i = 0; i < NUM_SENSORS; i++) {
    pinMode(xshutPins[i], OUTPUT);
    digitalWrite(xshutPins[i], LOW);
  }
  delay(50);

  for (int i = 0; i < NUM_SENSORS; i++) {

    // Turn ON this sensor only
    digitalWrite(xshutPins[i], HIGH);
    delay(50);

    if (!sensors[i].begin(0x29, false, &Wire)) {
      Serial.print("[ERROR] Sensor ");
      Serial.println(i);
      continue;
    }

    sensors[i].setAddress(sensorAddr[i]);

    sensors[i].configSensor(Adafruit_VL53L0X::VL53L0X_SENSE_HIGH_SPEED);

    sensors[i].startRangeContinuous();

    Serial.print("[OK] Sensor ");
    Serial.print(i);
    Serial.print(" addr: 0x");
    Serial.println(sensorAddr[i], HEX);
  }
}

void servo_setup() {
  ESP32PWM::allocateTimer(0);
  ESP32PWM::allocateTimer(1);
  ESP32PWM::allocateTimer(2);
  ESP32PWM::allocateTimer(3);

  servo.setPeriodHertz(50);
  servo.attach(SERVO_PIN, 1000, 2000);
}

void setup() {
  Serial.begin(115200);
  Wire.begin();
  Wire.setClock(400000);

  tof_setup();
  servo_setup();

  Serial.println("[READY]");
}

void loop() {
  handleSerial();
  updateServoSequence();

  for (uint8_t i = 0; i < NUM_SENSORS; i++) {

    if (sensors[i].isRangeComplete()) {
      uint16_t raw = sensors[i].readRange();

      if (raw > 0) {
        distances[i] = movingAverage(i, raw);
      }
    }
  }

  filterIndex = (filterIndex + 1) % FILTER_WINDOW;

  Serial.print(distances[2]);
  Serial.print(",");
  Serial.print(distances[1]);
  Serial.print(",");
  Serial.println(distances[0]);
}

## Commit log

2025-10-02 Add object distance and angle detection to color tracking
    Enhanced the Python script to calculate and display the distance and angle of detected red and green objects relative to the camera center, including a deadzone for central alignment. Also added an A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
2025-10-03 Integrate Arduino communication and motor control
    Enabled serial communication between Python and Arduino to send detected object color and angle. Updated Arduino code to parse messages, blink LED for 'RED' color to help with troubleshooting in the 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
2026-01-25 RPI camera support instead of USB webcam. Optimizations for running on PI4
2026-03-19 Delete Arduino code/Team-hot-glue-wro-arduino-code directory
    We have made a decision to not use Arduino as a microcontroller. Now all of that work is done using the rpi.
2026-03-24 Create a folder dedicated to CAD files
2026-04-14 Addinng and structuring CAD files. More information soon in README.
    [Battery_mount-001.step, Battery_mount-002.step, Battery_mount-003.step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]
2026-04-14 Rename Steering_V4.stp file for consistency
    [Steering_V4.stp]
2026-04-14 Add assembly instructions to README
    Added assembly beginning instructions for the robot
2026-04-14 Fix formatting of assembly instructions in README
2026-04-14 Fix fromating
    Added assembly instructions for robot construction.
2026-04-14 Fix fromating
    Added note about the strength of the plastic version of the chassis.
2026-04-14 Adding printable .stl files of the current version of robot chassis.
    [5v_conv_mount_asmbl.stl, 5v_converter_mount.stl, 5v_converter_stopper.stl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]
2026-04-18 Added wiring diagram
2026-04-18 Revise 3D printing instructions and add disclaimer
    Updated instructions for 3D printing the chassis and added a disclaimer regarding the 3D file source.
2026-04-18 Fix 3D file link and add authorship disclaimer
    Updated the link for the 3D file of the mBot2 chassis and added a disclaimer regarding authorship.
2026-04-18 Update assembly instructions in README
    Added steps for assembling the robot and included images.
2026-04-18 Update wiring diagram reference in README
2026-04-18 Format Wiring.pdf reference in README
2026-04-18 Enhance cable management instructions in README
    Added details about using CA glue for cable management.
2026-04-18 Enhance instructions for mounting electronic components
    Added details about securing the Raspberry Pi with velcro tape.
2026-04-18 Update chassis modification section in README
    Expanded on chassis modification details and painting options.
2026-04-20 Wiring diagrams directory
2026-04-21 wiring revision 3
2026-04-21 Added an IMU sensor
